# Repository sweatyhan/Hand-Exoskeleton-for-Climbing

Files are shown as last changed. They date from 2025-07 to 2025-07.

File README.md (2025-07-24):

# 说明文档（想到什么写什么）

## 目录  
1. 项目简介
2. 机械部分介绍
3. 嵌入式软件部分介绍
4. 嵌入式硬件部分介绍
5. 复现须知

## 1 项目简介
本项目是一对可以锁止的外骨骼手套（下称手套），用于在攀爬的过程中锁止，以节省攀爬者的体力，保证工作安全（至少课题是这么说的）。手套完全由手指驱动，只在感受到压力的情况下，由舵机驱动锁止，因此系统功耗极低，续航能力极强。据实测，舵机的功耗只有在锁止或者释放的时候会略超过3.7V*0.01A，其余时间均远小于该值。经过不严不松的注水分析，完全复现该项目所需要的物料成本可以控制在400以内，以满足+3分的课设要求。    
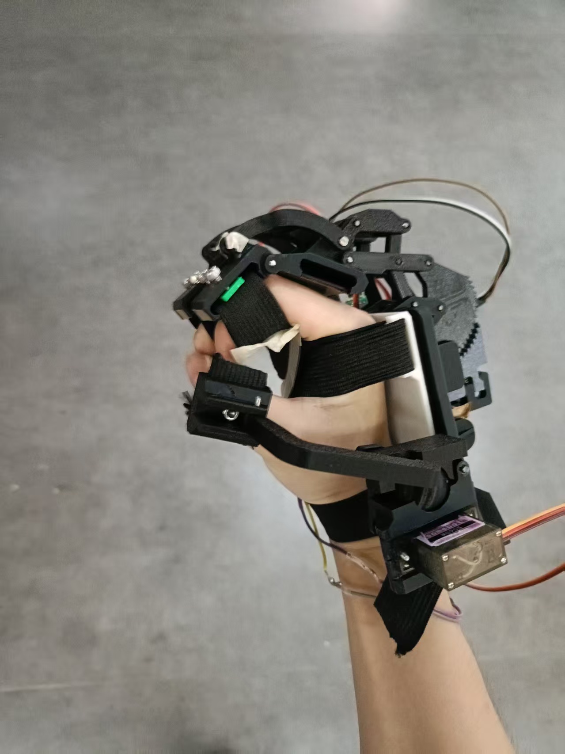
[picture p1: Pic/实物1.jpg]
  
手套主要有机械连杆部分（跟随手指移动）、机械锁止部分（用于锁住连杆）和嵌软控制部分组成。连杆的设计基本上完全参考另一开源项目https://github.com/ksDreamer/hand_exoskeleton ，并对其做了轻微的改变以适应新的需求。  

## 2 机械部分介绍

### 2.1 连杆
一个手套中的连杆包括食指和中指的1自由度连杆，以及拇指的2自由度连杆。因为课设要求每个手套只用做2根手指以上，所以就只为食指和中指这两根除拇指外力量最大的手指做了连杆。    

#### 2.1.1 食指、中指连杆
为了方便（那么代价是什么呢），本项目的食指连杆和中指连杆的参数完全一致，均来源于上述开源项目中的食指的参数。  

为了增强连杆结构的稳定性，把指节处的连接孔位相对上移，这样就不会和穿戴空间产生冲突，使得两边的连杆可以通过手指上方的一根长钢轴连接起来，而非分布于手指两侧的很短的钢轴或螺丝。这种设计也取消了连杆对于手指的全包围结构，使得手指在运动过程中不会受到两侧和下方的阻碍，感受更灵敏，适配的手指粗细范围更广。  
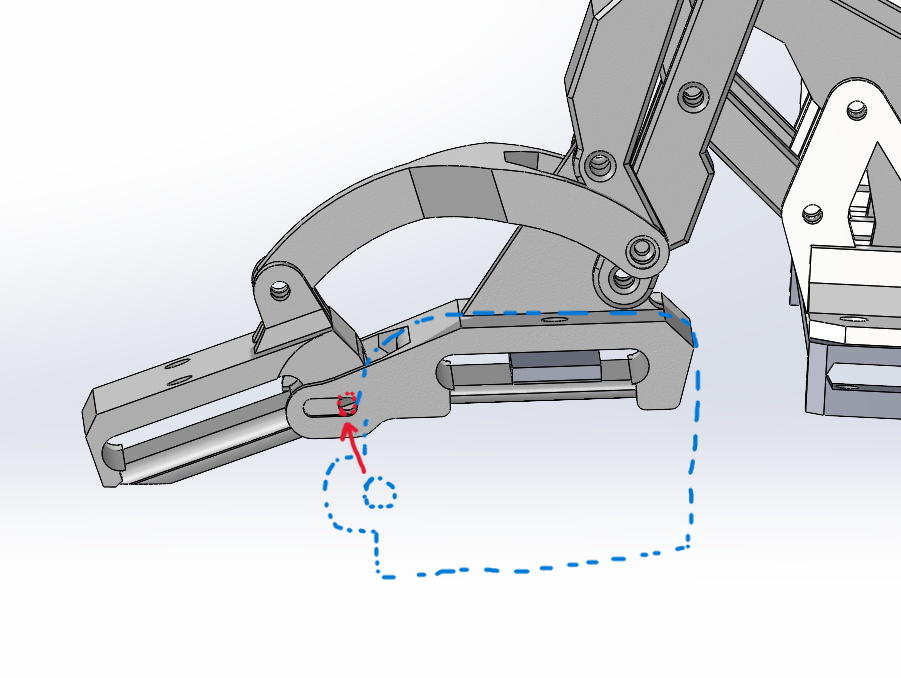
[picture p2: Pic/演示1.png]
   
上图展示了结构的变化。蓝色虚线部分表示原项目中连杆的实体投影，红色箭头表示连接孔位的移动方向  

除此之外，其余连杆均改进成了双端结构，极大提高了结构强度。

手指与连杆的穿戴采用弹力带。剪下一小段弹力带，将其穿过连杆中间的带槽，在确保头尾两端都在带槽中后，在带槽上方预留的两颗m3孔中拧入两颗m3*6/8的螺丝将弹力带压紧。  

#### 2.1.2 拇指连杆
未完待续

### 2.2 锁止机构
手指连杆的锁止使用棘轮方案实现。连杆的根部（也就是拳头那一块）呈大约1/4的棘轮形状，和另一轮廓与之啮合的活动锁止块相配合。活动锁止块由舵机带着前后移动，但并非与舵机直接连接，而是借由一个主动锁止块和弹簧弹性连接。活动锁止块与主动锁止块之间有机械限位，主动块对活动块的推力通过弹簧传递，拉力通过机械限位的结构传递，这样就能做到舵机在锁止时，带着主动块推动活动块向棘轮移动直到啮合；在释放时，带着主动块拉动活动块直到解除啮合。  

舵机与主动锁止块之间通过连杆连接。本项目中，为节省空间和降低功耗，食指和中指的外骨骼连杆的锁止和释放由一个舵机同时控制。由于主要结构都是PLA打印件，刚度较低容易形变，舵机在运动时难免因为受力而偏离原来的轴线，导致两根手指的活动锁止块运动不一致，经常是一根手指的外骨骼的棘轮啮合的非常紧，而另一根的棘轮还是松的。为解决这个问题，为舵机设计了一个双端连杆，以增大刚度，保证舵机的输出轴线一致。

### 3 嵌入式软件
欸嘿

### 4 嵌入式硬件
欸嘿

### 5 复现须知
#### 5.1 问题
由于更改了连杆的一部分参数而没有对其他参数做相对应的调整，连杆并不能完全跟随手指移动，这种情况对于中指更为严重，因为中指的参数和食指一致，但实际上中指比食指长，甚至会让手指关节顶到外骨骼，握紧的时候还挺痛的。   
 解决办法：
1 按比例适当增加中指外骨骼连杆的长度。具体的比例可能需要调整几次，最简单的办法是回到原项目https://github.com/ksDreamer/hand_exoskeleton 中把中指的连杆的数据全部测一遍（。然后再调整本项目每个连杆的零件的尺寸。本项目中每个连杆零件最基本的定义均是由连接孔位的相对位置确定（即最简化的连杆），所以参数还算好改，一般来说也不会报错  
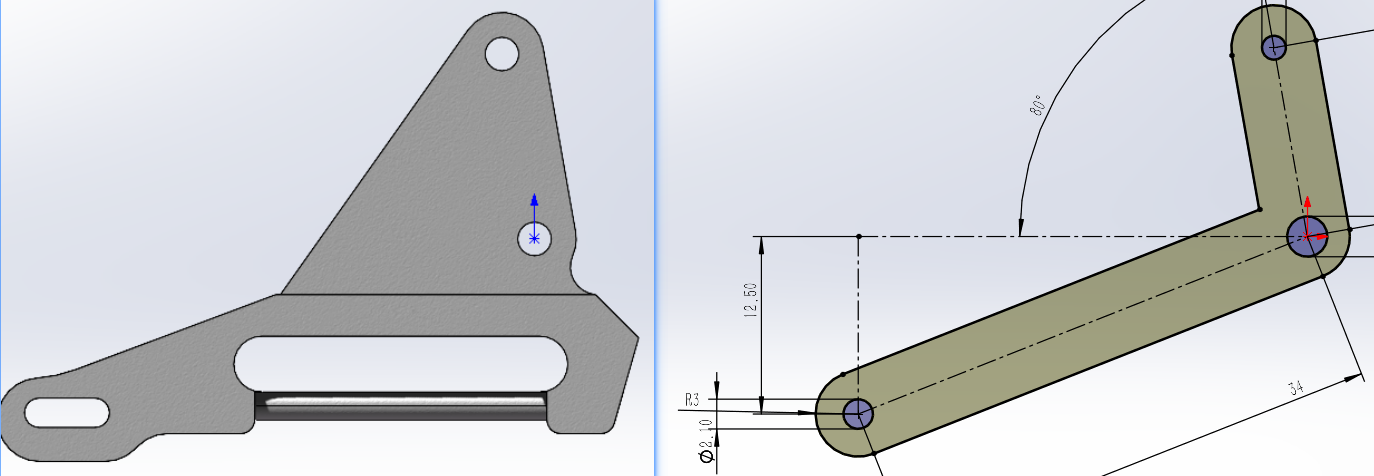
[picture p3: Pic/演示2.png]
     
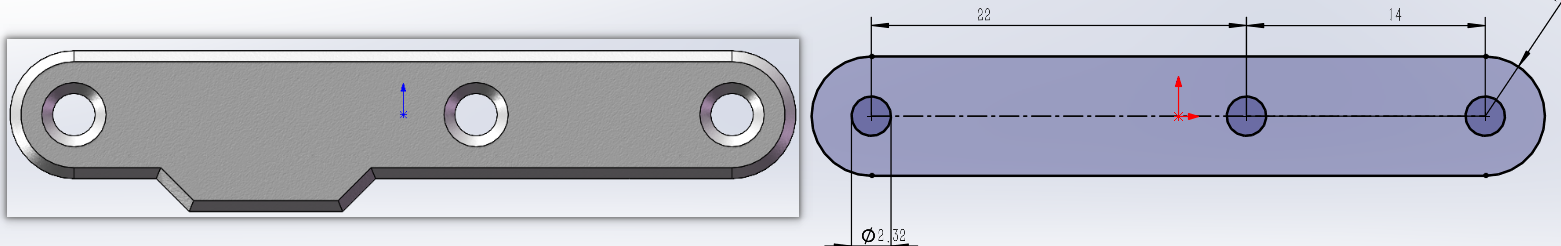
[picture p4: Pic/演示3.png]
   
2 微调连杆其他部分的参数，使得外骨骼整体上能始终与手指实际的运动保持一致，这就比较繁琐了，但是比较治本的方法  

#### 5.2 紧固件
装配使用的只有m3螺丝、m1.6塞打和m2钢轴，装配体中没有加入这些零件，但可以通过孔的特征判断对应的零件。孔径在3.2-3.4的对应m3螺丝；孔径在2.2-2.4或者还要大一点的，对应m2钢轴，只不过配合的松紧程度不一样；孔径小于2的，为塞打螺丝攻丝的部分，一个通孔由大孔和小孔组成，大孔厚度为1、孔径大于3.6，小孔孔径在2.7-2.9之间的，对应塞打螺丝的头部和肩部  

钢轴如果买的比较长需要剪，建议用大力钳https://e.tb.cn/h.hPxJwC1iw7pG1AI?tk=3KtQ4ejlVrz 这种，18-24寸的不赖。我们用的钢轴比较硬，很容易给大力钳卷刃，剪断之后的断面比较尖锐，打磨起来也比较费力，所以最好还是保证钢轴的长度差不多，可以修改连杆的厚度以适配钢轴，不过要保证厚度至少超过塞打螺丝的螺纹段长度。

#### 5.3 物料清单
BOM.xlsx中的物料清单供参考

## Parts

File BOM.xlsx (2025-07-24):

名字 | 金额 | 描述 | 规格 | 数量 | 链接
长条压力传感器 | -¥33.54 | 传感器 | RP-L-110 | 2 | https://e.tb.cn/h.hPKQ3cWlWupGRAR?tk=6jUv4e1LoMZ
电压转换模块 | -¥40.00 | 配合压力传感器使用 | 单路薄膜（串口版） | 2 | https://e.tb.cn/h.hPmAsELNnfKWNVy?tk=goX54e1ohHQ
弹簧 | -¥3.00 | 弹簧 | 0.3*3*10 | 1（包） | https://e.tb.cn/h.6xbCR7pFq2l455b?tk=3vk9VNw8DXE
舵机臂 | -¥19.64 | 舵臂 | 25T | 2 | https://e.tb.cn/h.6DE2cIYOi4wyJyo?tk=OBduVNwj1lu
舵机臂 | -¥13.82 | 舵臂 | 25T | 1 | https://e.tb.cn/h.6DE2cIYOi4wyJyo?tk=OBduVNwj1lu
耗材 | -¥35.90 | 3D打印耗材 | PLA | 1 | https://e.tb.cn/h.6DEdesVT8C1n3Xz?tk=h540VNwks2u
塞打螺丝 | -¥6.84 | 塞打螺丝 | M2.5*4*M1.6，M2.5*5*M1.6 | 1（包） | https://e.tb.cn/h.6DEdesVT8C1n3Xz?tk=h540VNwks2u
弹力带 | -¥8.80 | 弹力带 | 20mm | 1 | https://e.tb.cn/h.6xYdhplcbqLVmui?tk=xLPJVNwJ8T1
esp32 | -¥43.60 | esp32 | type-c口 FT232焊针38Pin | 2 | https://e.tb.cn/h.6DsUM9yRpx6XIFc?tk=4EB8VNwq1Ns
螺丝套装 | -¥21.50 | 螺丝套装 | m3，内六角 | 1（盒） | https://e.tb.cn/h.6xY12Mg7zsxf2Ym?tk=raCcVNwNUmu
杜邦线 | -¥7.34 | 杜邦线 | 3P | 10（条） | https://e.tb.cn/h.6DEeJxlQ4DmuVc9?tk=uRZrVNwMyCq
sg90 | -¥23.38 | 舵机 | MG90S | 2 | https://e.tb.cn/h.6xYc6mENdQ2MSMo?tk=seSMVNwoXzT
塞打螺丝 | -¥25.35 | 塞打螺丝 | M2.5*5*M1.6、M2.5*3*M1.6， | 1 | https://e.tb.cn/h.6DEdesVT8C1n3Xz?tk=h540VNwks2u
按键 | -¥3.27 | 无声按键 |  | 1（包） | https://e.tb.cn/h.hlXO5ns81DKMPEl?tk=mDrE4e1lOgp
钢轴 | -¥8.00 | 钢轴 | M2*70mm | 20 | https://e.tb.cn/h.hlaxQQcLkkv2za2?tk=q1Zm4ejietV
硬件 | -¥31.34 | 拓展板的元件 |  |  | 立创商城
 | 总计
 | -¥325.32

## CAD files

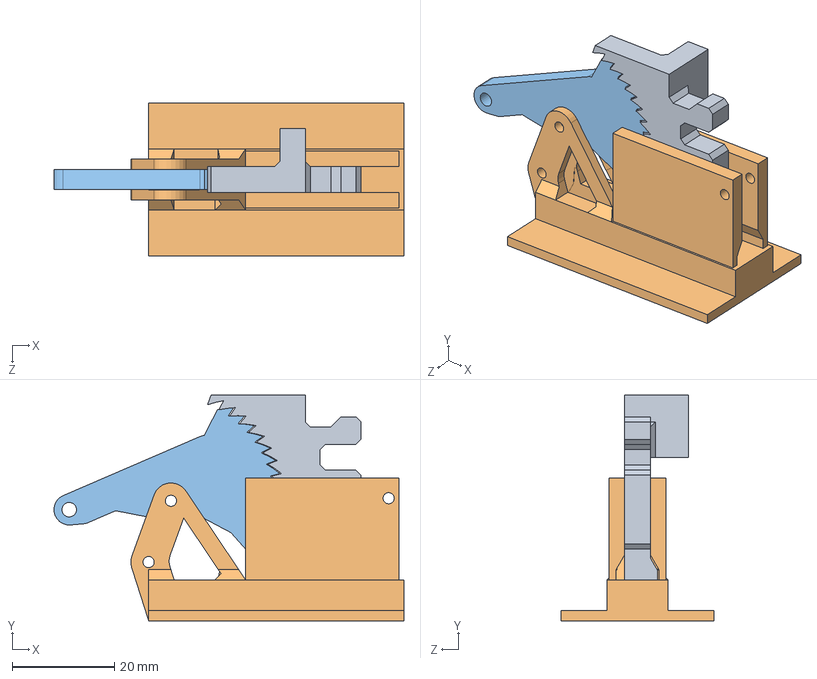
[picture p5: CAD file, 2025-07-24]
SW/零件/棘轮锁止.SLDASM
68.5 x 44.2 x 30.0 mm
杆3
杆4
棘轮锁止块2.0

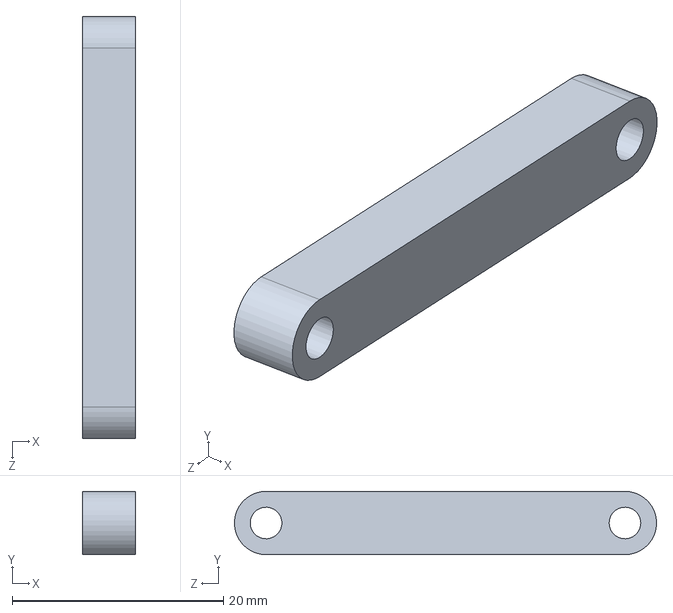
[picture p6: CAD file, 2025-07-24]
SW/零件/杆10.SLDPRT
5.00 x 6.00 x 40.0 mm

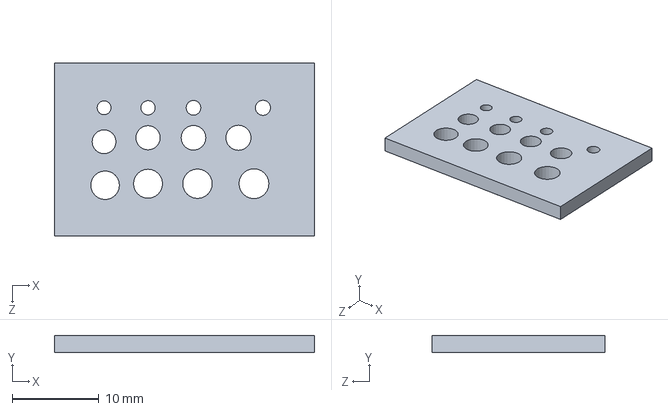
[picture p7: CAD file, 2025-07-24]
SW/零件/测试.SLDPRT
30.0 x 2.00 x 20.0 mm

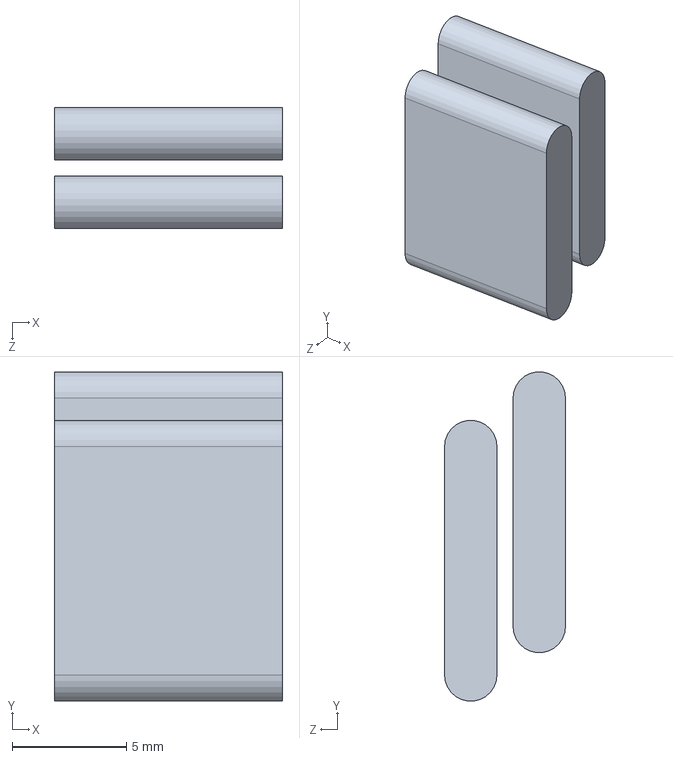
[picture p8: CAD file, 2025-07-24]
SW/零件/舵机草图.SLDPRT
10.0 x 14.4 x 5.30 mm

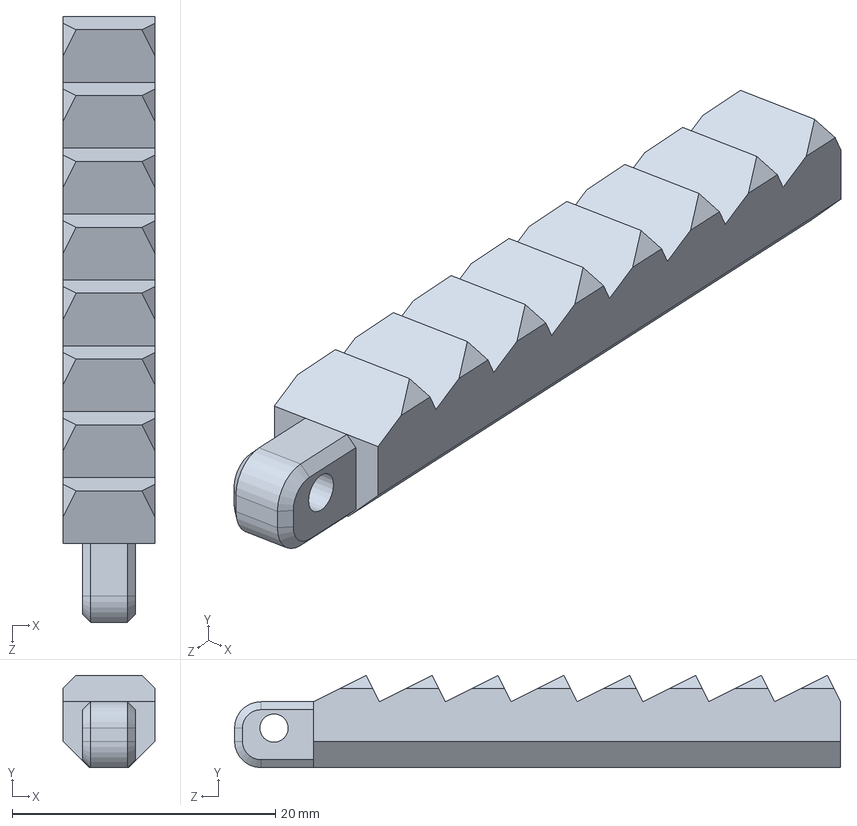
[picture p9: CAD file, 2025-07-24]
SW/零件/带齿杆1.SLDPRT
7.00 x 7.00 x 46.0 mm

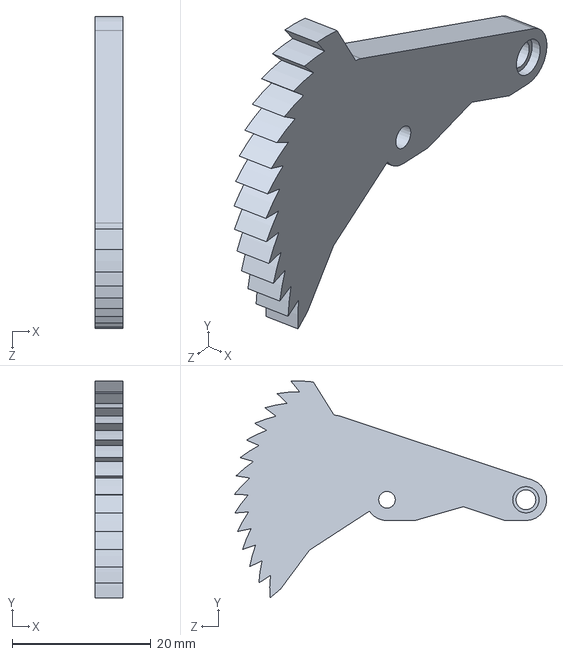
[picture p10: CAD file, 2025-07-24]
SW/零件/杆3.SLDPRT
4.00 x 31.2 x 45.0 mm

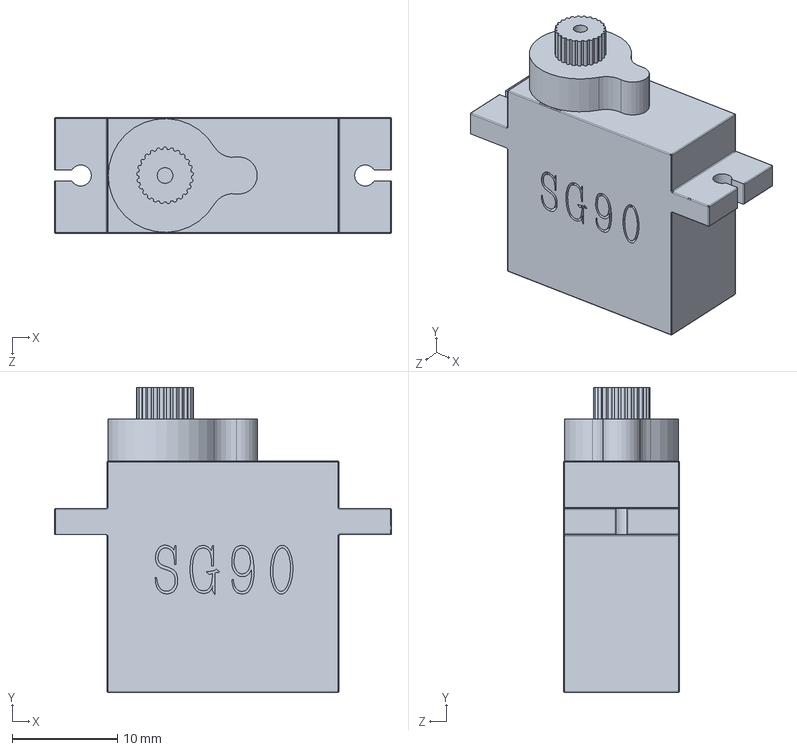
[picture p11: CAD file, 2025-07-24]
SW/零件/sg90.sldprt
32.0 x 29.0 x 11.0 mm

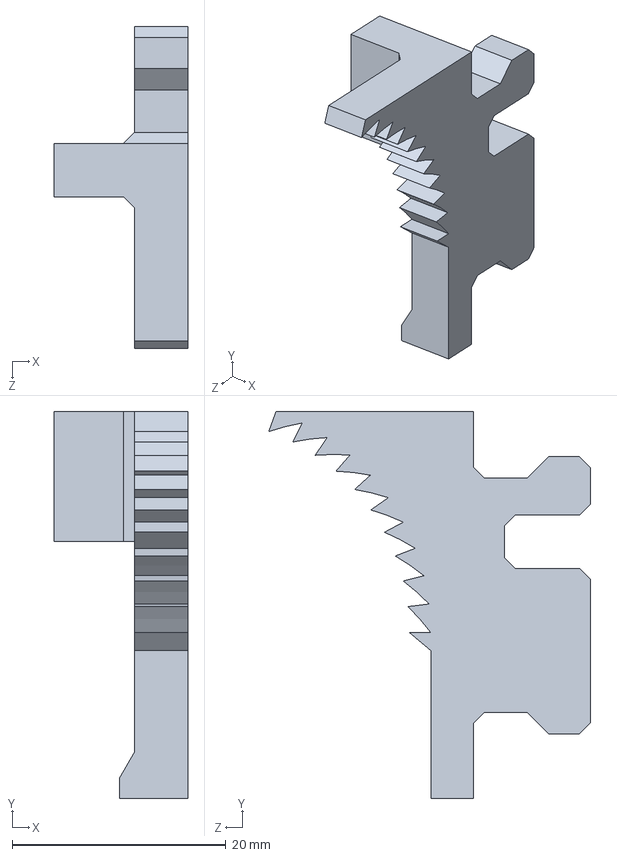
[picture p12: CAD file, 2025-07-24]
SW/零件/棘轮锁止块2.0.SLDPRT
12.5 x 36.2 x 30.1 mm

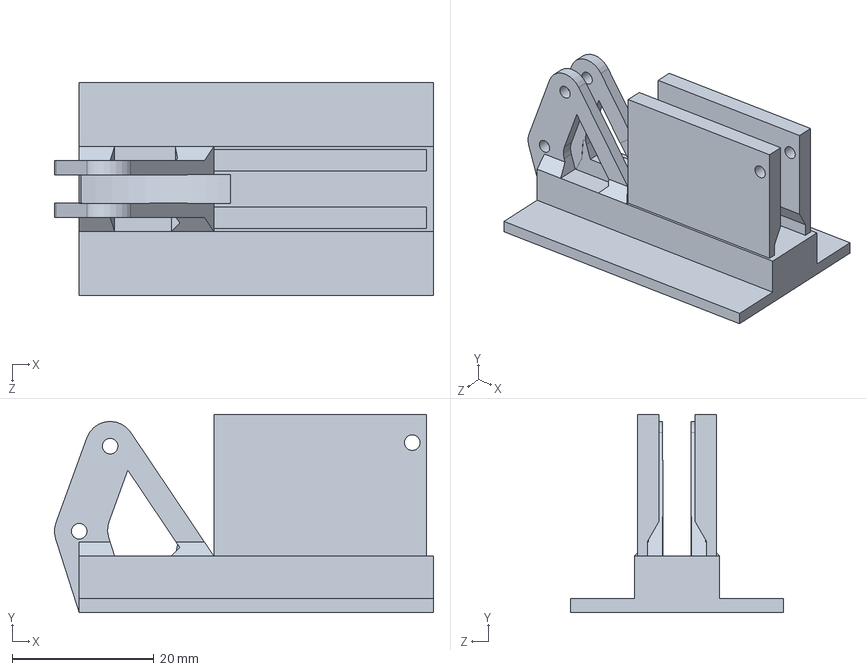
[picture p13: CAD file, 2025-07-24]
SW/零件/杆4.SLDPRT
53.5 x 28.0 x 30.0 mm

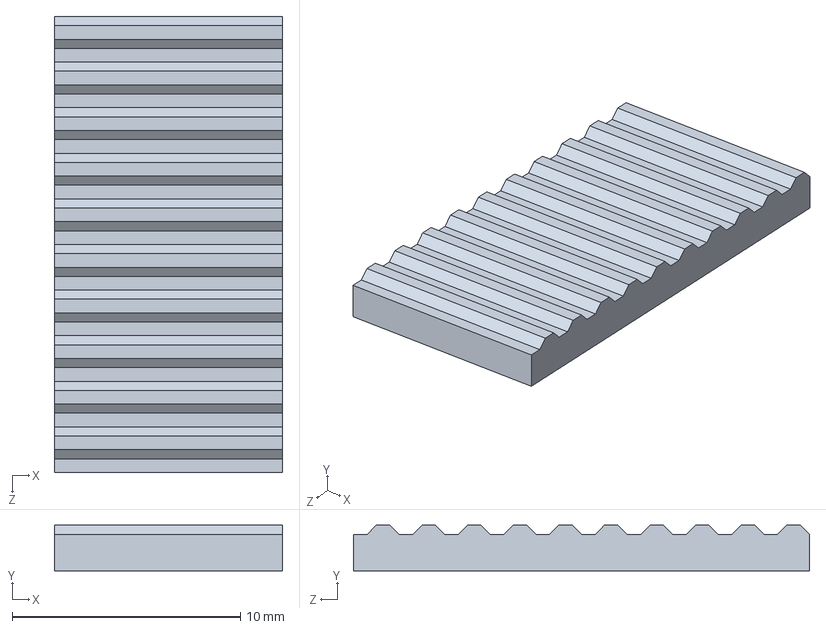
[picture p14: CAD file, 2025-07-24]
SW/零件/阻片.SLDPRT
10.0 x 2.00 x 20.0 mm

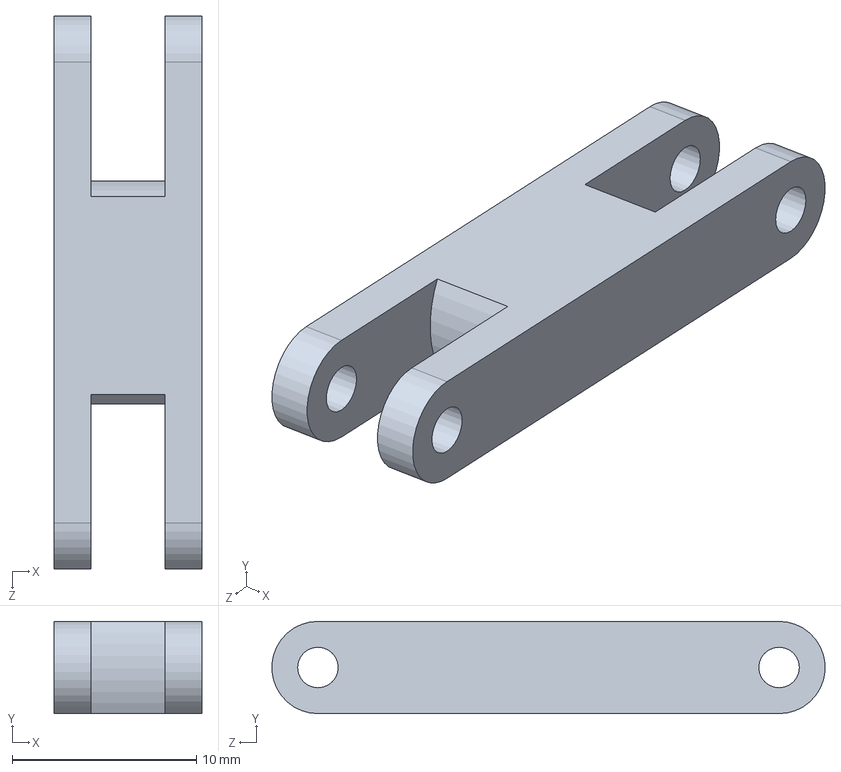
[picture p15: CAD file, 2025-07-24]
SW/零件/杆2.SLDPRT
8.00 x 5.00 x 30.0 mm

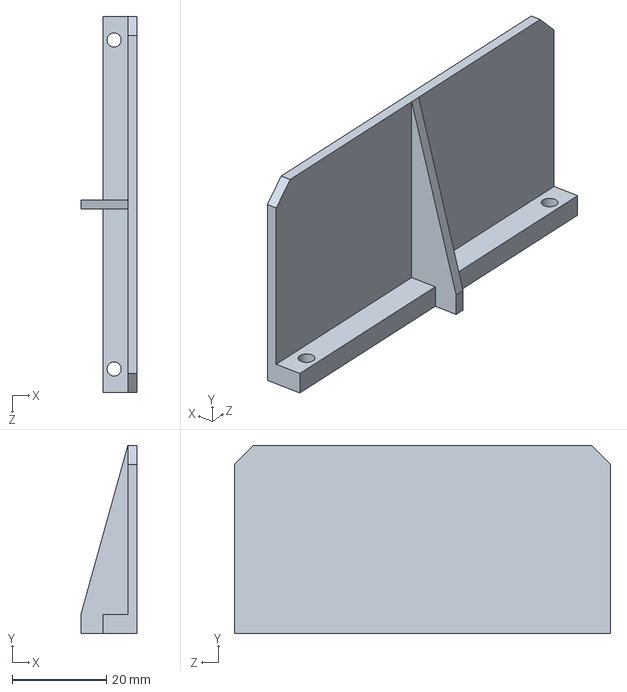
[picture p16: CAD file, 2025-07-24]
SW/零件/电控安装.SLDPRT
12.0 x 40.0 x 80.0 mm

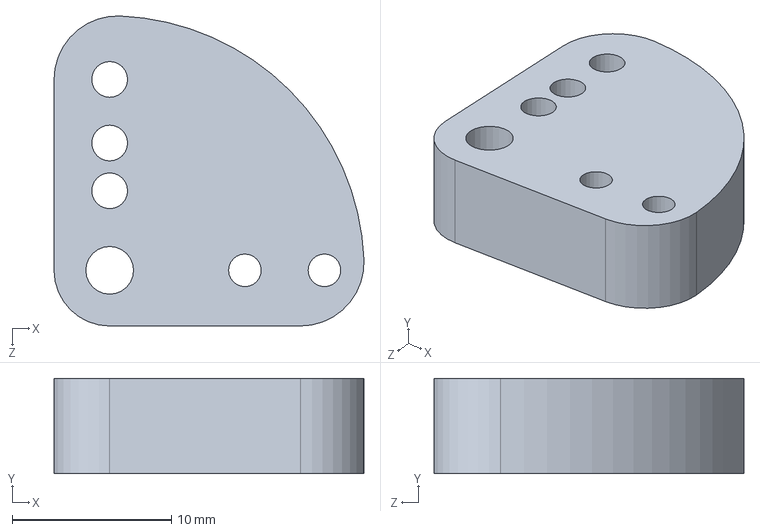
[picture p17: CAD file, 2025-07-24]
SW/零件/舵臂拓展臂.SLDPRT
19.5 x 6.00 x 19.5 mm

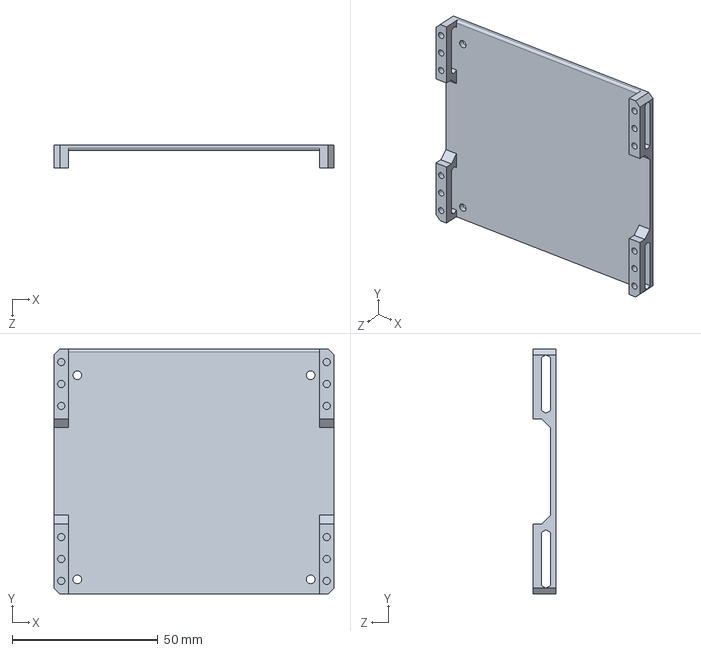
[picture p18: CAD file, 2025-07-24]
SW/零件/手套2.0.SLDPRT
96.0 x 84.0 x 8.00 mm

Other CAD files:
SW/零件/手套部分总装.SLDASM
SW/零件/Mirror杆11.1.1.SLDPRT
SW/零件/Mirror杆12.SLDPRT
SW/零件/连杆草图.SLDPRT
SW/零件/Mirror杆13.SLDPRT
SW/零件/Mirror棘轮锁止块2.0.SLDPRT
SW/零件/主动锁止块.SLDPRT
SW/零件/主动锁止块2.0.SLDPRT
SW/零件/圆柱销.SLDPRT
SW/零件/手套.SLDPRT
SW/零件/手背装甲.SLDPRT
SW/零件/杆11.1.1.SLDPRT
SW/零件/杆11.SLDPRT
SW/零件/杆12.SLDPRT
SW/零件/杆13.SLDPRT
SW/零件/杆6.2.SLDPRT
SW/零件/杆6.SLDPRT
SW/零件/杆7.SLDPRT
SW/零件/杆8.2.SLDPRT
SW/零件/杆8.SLDPRT
SW/零件/杆9.SLDPRT
SW/零件/棘轮.SLDPRT
SW/零件/活动锁止块.SLDPRT
SW/零件/測試圓柱.SLDPRT
SW/零件/舵机连杆.SLDPRT
SW/零件/舵臂.SLDPRT
SW/零件/舵臂接应.SLDPRT
SW/零件/锁止盖.SLDPRT
